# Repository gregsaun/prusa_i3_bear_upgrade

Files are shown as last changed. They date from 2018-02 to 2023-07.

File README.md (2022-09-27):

# Bear Frame Upgrade 2.1

## Table of contents
  1. [Introduction](#introduction)
  1. [Features](#features)
  1. [New features since Bear Frame 2.0](#new-features-since-bear-frame-20)
  1. [Compatibility](#compatibility)
  1. [Printed parts](#printed-parts)
  1. [Print settings](#print-settings)
  1. [Assembly guide](#assembly-guide)
  1. [Bill of materials](#bill-of-materials)
  1. [Optional parts](#optional-parts)
  1. [Community](#community)
  1. [Official distributors](#official-distributors)
  1. [Partners and contributors](#partners-and-contributors)
  1. [Support my work](#support-my-work)
  1. [Thank you](#thank-you)
  1. [License](#license)
  1. [Credit, sources and inspiration](#credit-sources-and-inspiration)

## Introduction

The Bear Frame Upgrade improves stiffness and reliability of the original [Prusa i3 MK2(S), MK2.5(S)(S+) and MK3(S)(S+)](https://www.prusa3d.com/). It allows faster prints, increases precision, makes maintenance easier and opens the door to more customisations. Plus it looks unique with our coloured frames!

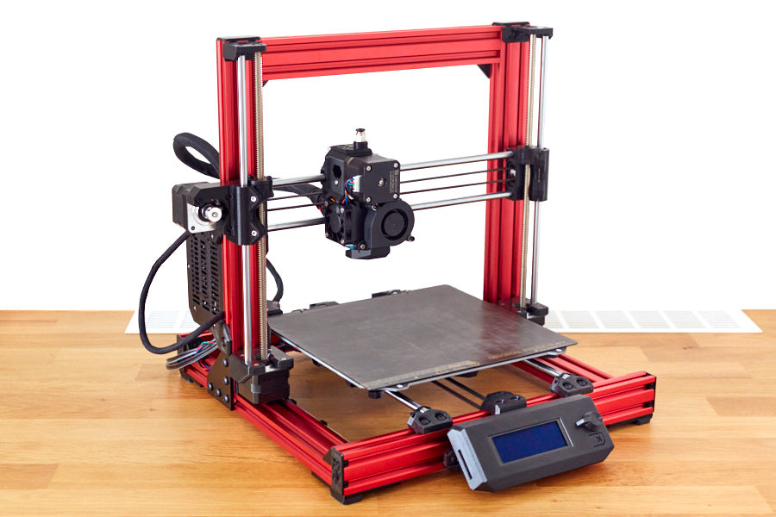
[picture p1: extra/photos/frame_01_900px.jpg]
Bear Frame Upgrade 2.1 MK3S


## Features

  * Compatible with Original Prusa i3 MK2(S), MK2.5(S) and MK3(S)(S+)
  * Compatible with lots of extruders like Original Prusa, BearExxa, BearMera (E3D Hemera) and Bondtech Prusa Upgrade
  * Reuse of as many parts as possible
  * Sturdy frame for faster printing
  * High quality extrusions
  * Custom, sturdier t-nuts
  * Improved accuracy
  * Reduced noise level
  * Easy to use and maintain
  * Built to last
  * Precisely engineered printed parts
  * Thoroughly tested development
  * Highly customisable
  * Detailed documentation via [guides.bear-lab.com](https://guides.bear-lab.com/)
  * Compatible with stock firmware (only if you use the Original Prusa extruder)
  * Active and open minded community
  * Truly open source

## New features since Bear Frame 2.0

  * Improved assembly guide and documentation (via [guides.bear-lab.com](https://guides.bear-lab.com/))
  * Single frame for all Prusa versions (same frame as Full Bear 2.0 MK3)
  * New stiffer Y axis with tensioner
  * New stiffer Z axis
  * Improved X and Y axis homing accuracy
  * Improved Z axis alignment and assembly
  * Reduced Y axis stepper noise for MK3(S)
  * New build helpers for Y and Z axis
  * Support for all Prusa PSUs
  * Custom, sturdier t-nuts
  * Shorter LCD supports
  * New custom LCD cover
  * Nicer and more resistant end caps
  * Easier assembly of printed parts
  * Improved wire management with new cable clips
  * Stiffer mounts for Rambo Mini/Einsy cover
  * Compatible with E3D Gates idlers as well as 9mm belt

## Compatibility

This Bear Frame Upgrade 2.1 is compatible with the Full Bear Frame Upgrade 2.0 __MK3__ frame. If you do not know which frame you have please check [our FAQ here](https://guides.bear-lab.com/Wiki/Bear_FAQ#Section_Which_Full_Bear_frame_do_I_have). The 2.1 version needs extra hardware (screws, nuts, washers, dowel pin), check the [bill of materials](doc/bom.md) for more details. You can also order hardware upgrade kit from our [distributor websites](#official-distributors).

:bulb: If you have a Full Bear Frame Upgrade 2.0 MK2S or MK2.5 frame you can find compatible parts in the [optional parts section](#optional-parts) below.

:warning: The new Y and Z axis are __not__ compatible with any of the existing Prusa or Bear 2.0 parts. You have to update all parts from Bear 2.1.

:warning: The original Prusa firmware is compatible with the Bear Upgrade 2.1 only if you use the Original Prusa extruder and X axis. If you use the Bear upgrade 2.1 frame with BearExxa, BearMera or Bondtech extruders you will need to use custom firmware.

## Printed parts

:bulb: All links here correspond to the latest stable release.

:warning: Warning: It is important to follow the recommended print settings and to **calibrate your extrusion multiplier** before printing the parts (for each and every spool that you use). [Check our calibration guide here](https://guides.bear-lab.com/Guide/Extrusion+multiplier+and+filament+diameter/8).

**Printed parts:**
  * Bear Frame 2.1 for MK3(S)(S+) STL files: [bear21_mk3-3s_stl.zip](../../releases/latest/download/bear21_mk3-3s_stl.zip)
  * Bear Frame 2.1 for MK2(S) or MK2.5(S) STL files: [bear21_mk2-2s-25-25s_stl.zip](../../releases/latest/download/bear21_mk2-2s-25-25s_stl.zip)
  * Bear Frame 2.1 optional parts (check [optional parts section](#optional-parts) below) files: [bear21_optional_parts.zip](../../releases/latest/download/bear21_optional_parts.zip)

**CAD, drawings and source files**:
  * Bear 2.1 frame for MK3(S)(S+) CAD files and mechanical drawings: [bear21_cad_drawings_files.zip](../../releases/latest/download/bear21_cad_drawings_files.zip)
  * All source files (this complete repository): Go the to latest release [here](../../releases/latest) and in the bottom of the release note, under the Assets, click on "Source code" (you can choose between zip and tar.gz files).

## Print settings

:warning: Warning: It is important to follow the recommended print settings and to **calibrate your extrusion multiplier** before printing the parts (for each and every spool that you use). [Check our calibration guide here](https://guides.bear-lab.com/Guide/Extrusion+multiplier+and+filament+diameter/8).

[Read the print settings here](doc/print_settings.md).

## Assembly guide

[Read the assembly guide here](https://guides.bear-lab.com/c/Frame).

## Bill of materials

[Read the BOM here](doc/bom.md).

## Optional parts

#### Official optional parts

| Description | Link |
|---|---|
| Upgrade parts for Bear 2.0 MK2(S), MK2.5(S) frame | [bear_2.0_upgrade_mk2-2s-2.5-2.5s](optional_parts/bear_2.0_upgrade_mk2-2s-2.5-2.5s/README.md) |
| LCD cover | [lcd_cover](optional_parts/lcd_cover/README.md) |
| MMU2(S) frame holder adapter | [mmu2_adapter](optional_parts/mmu2_adapter/README.md) |
| Y idler for larger 9mm 2GT belt | [y_idler_9mm_belt](optional_parts/y_idler_9mm_belt/README.md) |
| Y idler tensioner for E3D idler | [y_idler_tensioner_e3d](optional_parts/y_idler_tensioner_e3d/README.md) |
| Bear Extruder and X Axis | [Bear Extruder and X axis for MK2.5S MK3S](https://github.com/gregsaun/bear_extruder_and_x_axis) |

#### Community's optional parts

Find optional parts designed by the community at [guides.bear-lab.com/Wiki/community_optional_parts](https://guides.bear-lab.com/Wiki/community_optional_parts).

## Community

Here are the places were The Bear project is the most active on:

* Discord server of "The 602 Wasteland" community : [discordapp.com/invite/hYUjSnW](https://discordapp.com/invite/hYUjSnW)
* Facebook group : [facebook.com/groups/PrusaBearUpgrade](https://www.facebook.com/groups/PrusaBearUpgrade)
* Twitter : [@gregoiresaunier](https://twitter.com/gregoiresaunier)
* GitHub : [github.com/gregsaun](https://github.com/gregsaun)

Do not hesitate to ask if you have a question.

## Official distributors

Official distributors are selling the official bear kit with all screws, our custom t-nuts and extrusions ready for the upgrade from an Original Prusa, you will only need to print 3D printed parts.

  * 3dboom.es logo  
    3D Boom (EU)  
    [3dboom.es](http://www.3dboom.es)  

  * lecktor logo  
    Lecktor (EU)  
    [lecktor.com](http://lecktor.com)  

  * makerparts.ca logo  
    Makerparts.ca (CA)  
    [makerparts.ca](http://makerparts.ca)  

  * ooznest logo  
    Ooznest (UK)  
    [ooznest.co.uk](https://ooznest.co.uk/)  

  * printed solid logo  
    Printed Solid (US)  
    [printedsolid.com](https://www.printedsolid.com/)  

By purchasing a kit from official distributors you are supporting the development of the Bear project, thank you very much :heart: !

## Partners and contributors

LDO Motors &nbsp;[LDO Motors](http://ldomotors.com/) is the manufacturer of the official Bear frame upgrade kit for all distributors.

3DFused &nbsp;[3DFused](https://3dfused.com/) is helping the Bear development team with linear motion knowledge and will sell custom linear rail kit for the Bear Frame Upgrade.

Grégoire Saunier is the original designer of the Bear Frame Upgrade and Extruder.

Bendix Sørensen, David Ogles, Florian Däubler, Josh Jones and Stefan Maue are active contributors.

Barry Danks, David Ogles, Florian Däubler, Josh Jones, Nathan Denkin, Orlando from All3DMakers and Termlimit are admins of the Bear community and help with documentation.

## Support my work

The bear project is made possible thanks to its supporters. You can participate via
<br/><br/>
become a patron (https://www.patreon.com/gregsaun)<br/>[patreon.com/gregsaun](https://www.patreon.com/gregsaun)
<br/><br/>
paypal.me (https://www.paypal.me/gregsaun)<br/>[paypal.me/gregsaun](https://www.paypal.me/gregsaun)
<br/><br/>
You can also send me a tip via [Thingiverse](https://www.thingiverse.com/pekcitron/about) if you prefer.

Massive thank you in advance :heart:

## Thank you

Massive thank you to [Adrian Bowyer](https://github.com/AdrianBowyer/) for having invented [RepRap](http://reprapltd.com).

Thank you to all [my Patreon's](https://guides.bear-lab.com/Wiki/Bear_Supporters)

Thank you to Bendix Sørensen, David Ogles, Florian Däubler, Jason from LDO Motors, Nathan Denkin, Orlando from All3DMakers, Sleene, Termlimit, Josh Jones and Stefan Maue for helping me in developing the Bear project and for their beautiful support to the community.

Thank you to all that have sent me a tip on Thingiverse and PayPal.

Thank you to everybody from our Facebook group and The 602 Wasteland community.

Thank you for having purchased a kit from an official distributor.

Thank you to all official distributors for taking care of the kits and customers.

Thank you Jason from LDO Motors for the quality manufacturing and relationship.

Thank you Openbuilds<sup>&reg;</sup> for your hardware, community and state of mind.

Thank you for making the community alive with all your comments, issues, pull requests, optional parts, make, pictures, etc.

## License

All files in this repository are licensed under the GPLv3 license (unless otherwise noted). Here is a quick summary; for more details please check the LICENSE file.

What you __can__ do:
  * Modify
  * Distribute
  * Private, commercial and patent use

What you __must__ do:
  * Include copyright notice
  * Include a copy of the license
  * Share source files
  * Use the same license (GPLv3)
  * Document changes applied

Note: STL and STEP files are generally not source files. The source files are those you use to design your project such as CAD files (Fusion 360), mechanical drawings, code, documentation, etc. However, STL and STEP files are a commonly used format with great interoperability. Therefore, we encourage to share the STL and STEP files in addition to the source files.

## Credit, sources and inspiration

  * [Adrian Bowyer](https://github.com/AdrianBowyer/) for having invented [RepRap](http://reprapltd.com).
  * Original Prusa i3 printers: [prusa3d.com](http://www.prusa3d.com).
  * Prusa 3030 Haribo Edition: [github.com/PrusaMK2Users/3030_Haribo_Edition](https://github.com/PrusaMK2Users/3030_Haribo_Edition).
  * Openbuilds<sup>&reg;</sup> for the invention of open source V-Slot<sup>&reg;</sup> extrusions : [openbuilds.org](https://www.openbuilds.org).
  * Roy Henriksson for the inspiration of his Y axis tensioner : [thingiverse.com/thing:3502543](https://www.thingiverse.com/thing:3502543).
  * Vecko Kojchevski for his Z axis parts and feedback : [thingiverse.com/vekoj/designs](https://www.thingiverse.com/vekoj/designs).

Massive thanks to these persons and projects, without them the Bear could not exist!

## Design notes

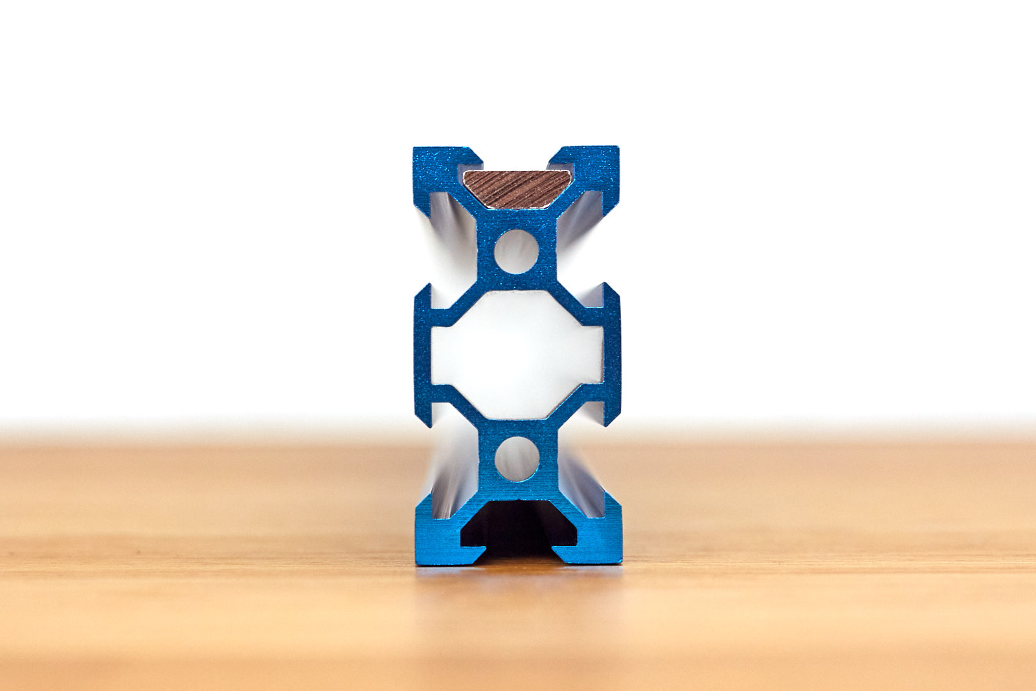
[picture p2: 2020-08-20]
extra/photos/hardware_08.jpg

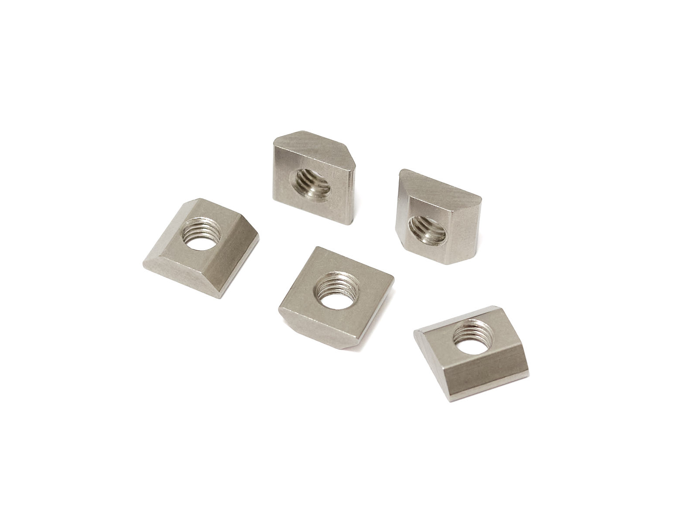
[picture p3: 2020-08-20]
extra/photos/hardware_02.jpg

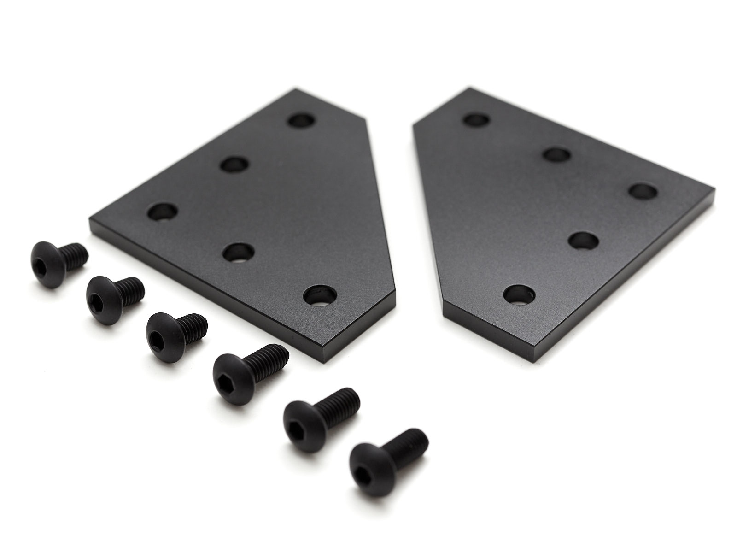
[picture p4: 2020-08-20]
extra/photos/hardware_03.jpg

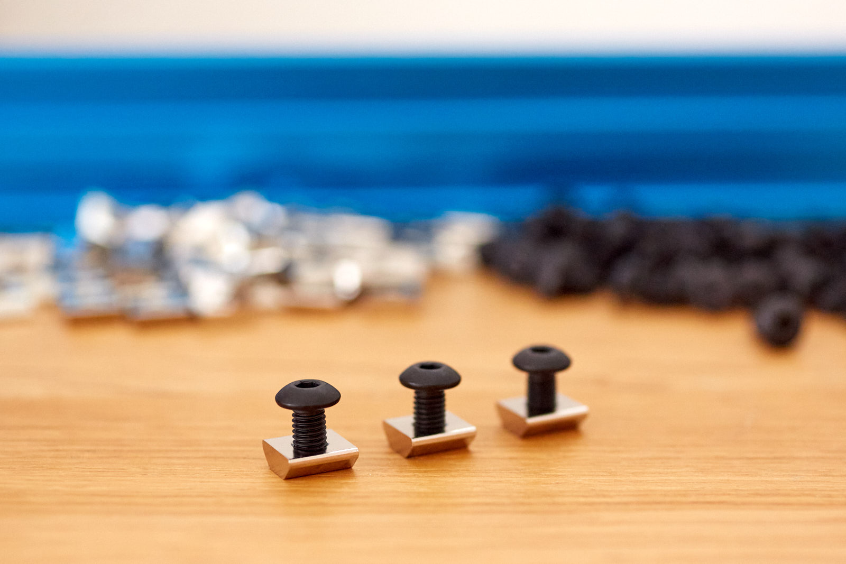
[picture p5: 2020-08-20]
extra/photos/hardware_06.jpg

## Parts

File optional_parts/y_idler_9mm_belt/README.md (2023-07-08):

# Bear Frame Upgrade 2.1

## Y idler for 9mm belts

### Introduction

This is a Y idler for 9mm wide Gates 2GT belt (standard is 6mm). Larger belts will have less flex and might reduce ringing.

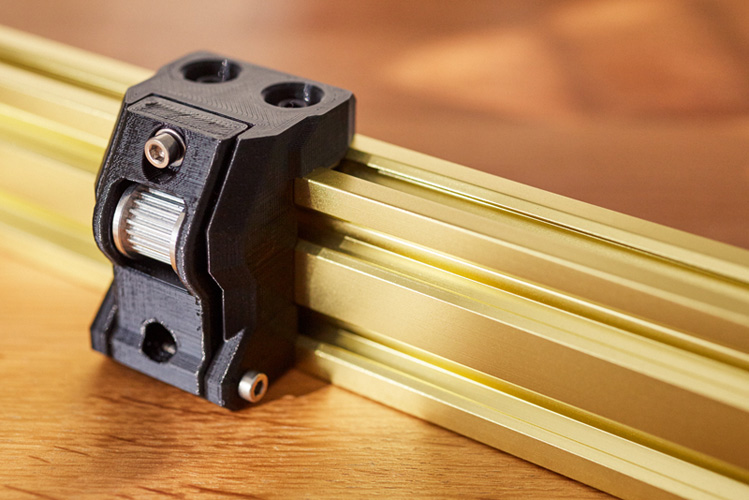
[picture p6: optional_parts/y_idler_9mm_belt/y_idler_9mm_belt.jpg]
Y idler for 9mm 2GT belt


### Bill of Materials

| Part | Quantity | Detail |
|---|:---:|---|
| E3D Gates 2GT 9mm Belt | 1 | [E3D store link](https://e3d-online.com/gates-powergripr-gt2-belt-9mm-x-100mm) |
| E3D Gates 2GT Toothed Idler<br/>9mm Belt, 20 Tooth, 5mm bore | 1 | [E3D store link](https://e3d-online.com/products/gates-belts-pulleys-and-idlers?variant=41205372420155) |
| 2GT Pulley 16T, 5mm bore | 1 | [Aliexpress Powge store](https://www.aliexpress.com/item/32995138803.html) |
| Dowel pin<br/>diameter: 4.90-4.95mm<br/>length: 20mm | 1 | Must fit the 2GT idler bearing.<br/>:pushpin: Cut a M5 screw if you can't find one |
| M3x30mm socket head screw ISO 4762 | 1 | |
| M3x25mm socket head screw ISO 4762 | 1 | |
| M3 Hex nylock nuts (DIN 985) | 2 | |
| M3 steel washer DIN 125, 0.5mm thick | 1 | |

### Printed parts

:pushpin: If you have any doubt as to which Bear frame you have, please check the [Bear FAQ here](https://guides.bear-lab.com/Wiki/Bear_FAQ#Section_Which_Bear_frame_do_I_have).

:warning: Warning: It is important to follow the recommended print settings and to **calibrate your extrusion multiplier** before printing the parts (for each and every spool that you use). [Check our calibration guide here](https://guides.bear-lab.com/Guide/Extrusion+multiplier+and+filament+diameter/8).

| Part | Qty | Note | Download link |
|---|:---:|---|---|
| y_belt_holder_9mm_belt_bear2.0_mk2s-2.5-2.5s | 1 | :warning: For Bear 2.0 MK2(S), MK2.5(S) frame | [y_belt_holder_9mm_belt_bear2.0_mk2s-2.5-2.5s.stl](printed_parts/y_belt_holder_9mm_belt_bear2.0_mk2s-2.5-2.5s.stl?raw=true) |
| y_belt_holder_9mm_belt_bear2.1_mk2s-2.5-2.5s | 1 | :warning: For Bear 2.1 MK2(S), MK2.5(S) frame | [y_belt_holder_9mm_belt_bear2.1_mk2s-2.5-2.5s.stl](printed_parts/y_belt_holder_9mm_belt_bear2.1_mk2s-2.5-2.5s.stl?raw=true) |
| y_belt_holder_9mm_belt_bear2.1_mk3-3s | 1 | :warning: For Bear 2.1 MK3(S) frame | [y_belt_holder_9mm_belt_bear2.1_mk3-3s.stl](printed_parts/y_belt_holder_9mm_belt_bear2.1_mk3-3s.stl?raw=true) |
| y_idler_mount_9mm_belt | 1 | | [y_idler_mount_9mm_belt.stl](printed_parts/y_idler_mount_9mm_belt.stl?raw=true) |
| y_idler_tensioner_9mm_belt | 1 | | [y_idler_tensioner_9mm_belt.stl](printed_parts/y_idler_tensioner_9mm_belt.stl?raw=true) |

The Y motor mount from the standard Bear Frame 2.1 printed parts is reused.

### Print settings

:warning: Warning: It is important to follow the recommended print settings and to **calibrate your extrusion multiplier** before printing the parts (for each and every spool that you use). [Check our calibration guide here](https://guides.bear-lab.com/Guide/Extrusion+multiplier+and+filament+diameter/8).

  * Slicer : PrusaSlicer recommended
  * Infill type : Gyroid recommended
  * Support : No
  * Brim : No
  * Detect thin walls : No
  * Perimeters width (internal and external) : 0.45mm

| Part | Layer<br/>Height<br/>[mm] | Infill [%] | Num.<br/>Perimeters | Num.<br/>Top/Bottom<br/>Layers |
|:-----|:---:|:---:|:---:|:---:|
| y_belt_holder_9mm_belt_X | 0.20 | 20 | 4 | 5 |
| y_idler_mount_9mm_belt | 0.20 | 20 | 4 | 5 |
| y_idler_tensioner_9mm_belt | 0.20 | 20 | 4 | 5 |

### Assembly instructions

Follow the same assembly instructions as for the standard Bear 2.1 Y idler.

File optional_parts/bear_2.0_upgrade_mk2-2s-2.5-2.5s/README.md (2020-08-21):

# Bear Frame Upgrade 2.1

## Bear 2.1 upgrade parts for use on an original Full Bear 2.0 MK2(S)/MK2.5(S) frame

### Table of contents
  1. [Introduction](#introduction)
  1. [Printed parts](#printed-parts)
  1. [Print settings](#print-settings)
  1. [Assembly guide](#assembly-guide)
  1. [Bill of materials](#bill-of-materials)

### Introduction

These parts allow you to upgrade your __Full Bear 2.0 MK2(S)/MK2.5(S) frame__ to use similar parts to, and with the same features as, the Bear 2.1 parts. The new Bear 2.1 frame is based on the Full Bear 2.0 MK3 frame which has (some) different extrusion lengths to the Full Bear 2.0 MK2(S)/MK2.5(S) frame.

These parts are __not__ compatible with the __Bear 2.1 frame for Prusa MK2(S)/MK2.5(S)__.

### Printed parts

To confirm that you have a __Full Bear 2.0 MK2(S)/MK2.5(S) frame__, you just need to check the length of the Y axis extrusions.

Measure the length of your Y axis __extrusion__ as shown in the diagram below.
  * If the length is __311 mm__ (±1mm):
    * Then you have a __Full Bear 2.0 MK2(S)/MK2.5(S) frame__.
    * You will need to use these parts: [Download this ZIP file](../../../../releases/latest/download/bear21_optional_parts.zip), STL are in the folder `bear_2.0_upgrade_mk2-2s-2.5-2.5s/printed_parts/stl`.
  * If the length is __331 mm__ (±1mm):
    * Then you have a frame compatible with the Bear 2.1 parts. You do __not__ need to use any of the parts linked above. Download the printed parts from the [links on the main, Bear 2.1, page](../../README.md#printed-parts).

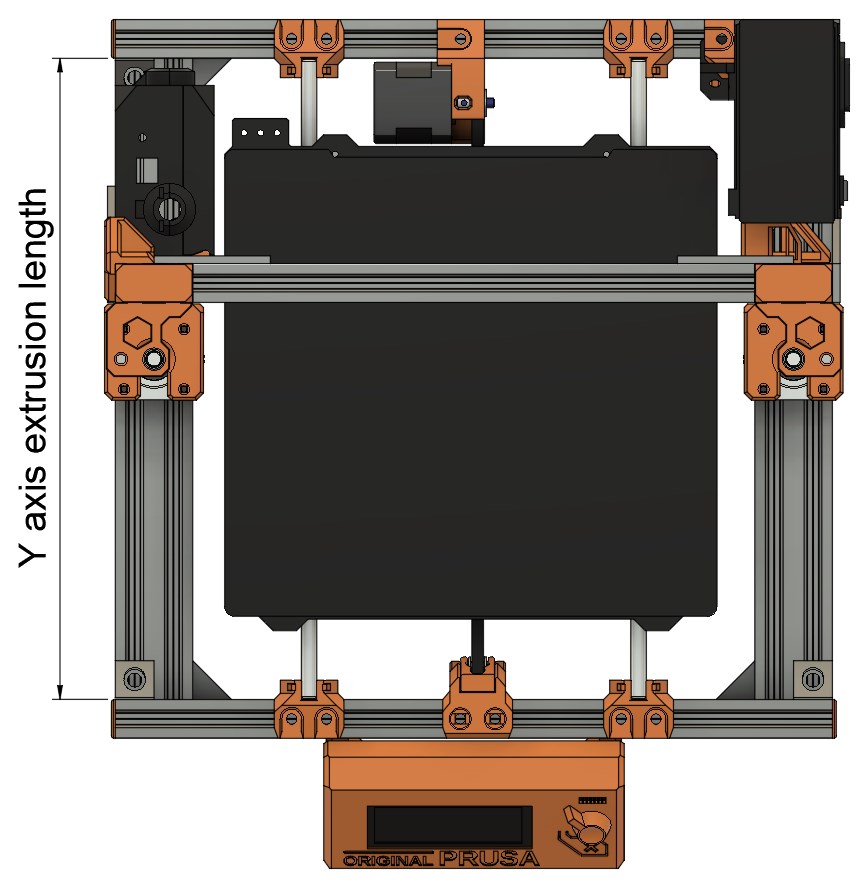
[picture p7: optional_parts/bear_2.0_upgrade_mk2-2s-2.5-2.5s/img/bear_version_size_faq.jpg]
Bear version frame size


### Print settings

:warning: Warning: It is important to follow the recommended print settings and to **calibrate your extrusion multiplier** before printing the parts (for each and every spool that you use). [Check our calibration guide here](https://guides.bear-lab.com/Guide/Extrusion+multiplier+and+filament+diameter/8).

Use the same print settings as for the Bear Frame 2.1 parts: [link to the print settings](../../doc/print_settings.md).

### Assembly guide

Use the same assembly guide as for the Bear Frame 2.1: [link to the assembly guide](https://guides.bear-lab.com/c/Frame).

### Bill of materials

The BOM is the same as for the Bear Frame 2.1: [link to the bom](../../doc/bom.md).

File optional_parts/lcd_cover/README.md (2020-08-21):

# Bear Frame Upgrade 2.1

## LCD Cover

### Table of contents
  1. [Introduction](#introduction)
  1. [Pictures](#pictures)
  1. [Compatibility](#compatibility)
  1. [Bill of materials](#bill-of-materials)
  1. [Printed parts](#printed-parts)
  1. [Print settings](#print-settings)

### Introduction

This is an alternative LCD cover designed for the Bear Frame Upgrade.
  * New accurate design from scratch
  * Shorter frame thanks to a bevel at the front (4th picture)
  * Elimination of vibrations by using 4 screws to attach the LCD
  * Easier rotation of the LCD knob
  * Faster to print while using less filament
  * Sleek design for better look
  * Improved design for best print quality
  * Optional: LCD supports compatible with stock Prusa MK3(S) frame
  * Available in several looks:
      * Simple without text or logo
      * Bear logo
      * Bear Upgrade text
      * Bear logo and text
      * Bear Paw logo

:bulb: The Bear Paw logo is a special design for the LGBT community because it is one of their symbols. You can find more details about it here: https://en.wikipedia.org/wiki/Bear_flag_(gay_culture)

### Pictures

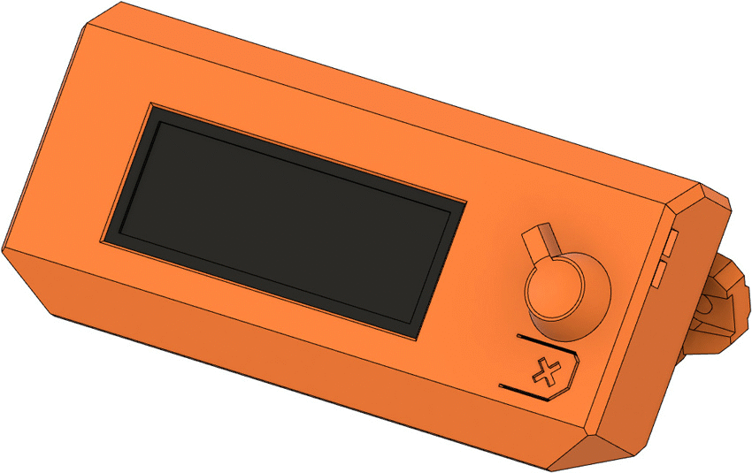
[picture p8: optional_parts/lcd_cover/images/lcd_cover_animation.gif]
LCD Cover Animation


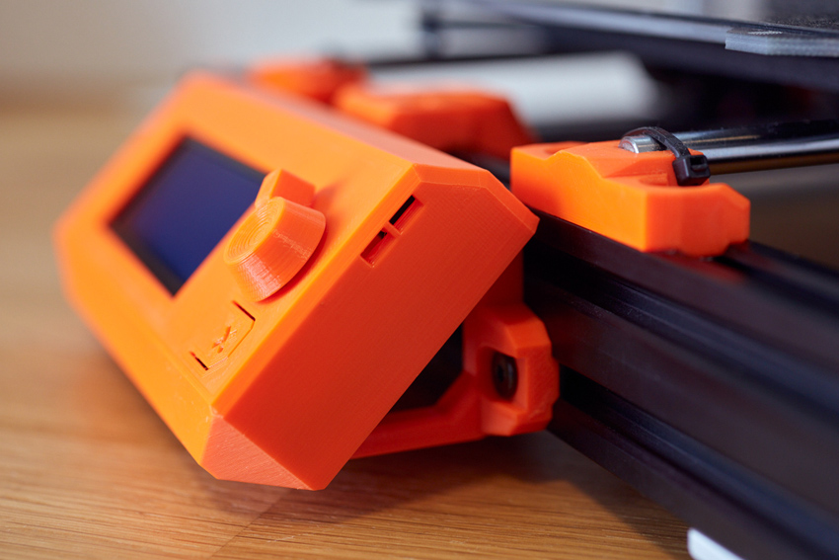
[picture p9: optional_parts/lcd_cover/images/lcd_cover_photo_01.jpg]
LCD Cover Photo speaker holes


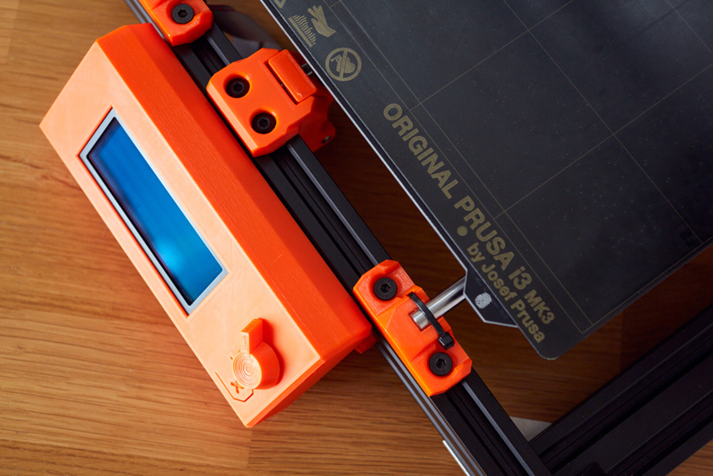
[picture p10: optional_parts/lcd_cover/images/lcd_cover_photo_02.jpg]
LCD Cover Photo top view


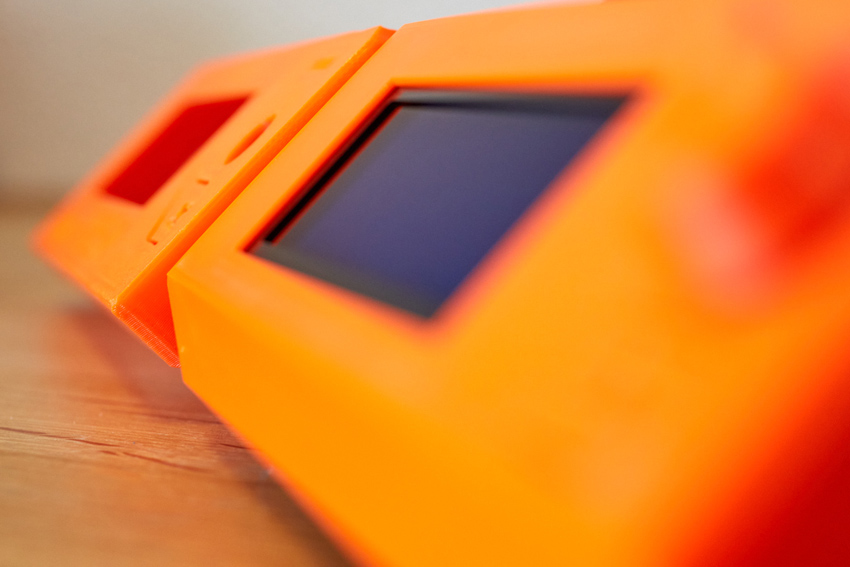
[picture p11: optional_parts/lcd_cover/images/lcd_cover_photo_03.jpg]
LCD Cover Photo bevel


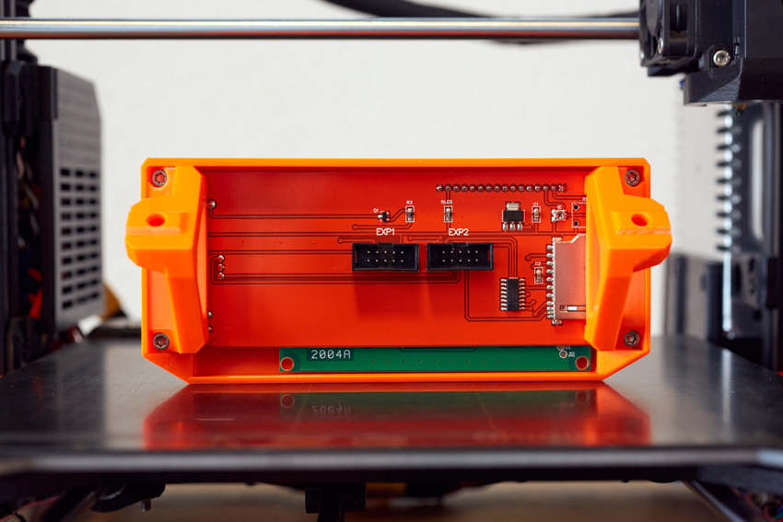
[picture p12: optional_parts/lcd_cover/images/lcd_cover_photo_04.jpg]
LCD Cover Photo screw mount


# Compatibility

This Bear LCD cover is compatible with all Bear Frame Upgrades. It is also compatible with the Original Prusa MK3(S) frame (see section [Printed parts](#printed-parts)).

### Bill of materials

| Part | Quantity | Detail |
|---|:---:|---|
| Original Prusa LCD unit | 1 | [Prusa store link](https://shop.prusa3d.com/en/spare-parts/213-lcd-unit.html) |
| M3x10mm socket head screw ISO 4762 | 4 | |

### Printed parts

| Part | Qty | Note | Download link |
|---|:---:|---|---|
| lcd_cover | 1 |  Choose one of the available designs (check the GIF on top) | [lcd_cover.stl](printed_parts/stl/lcd_cover.stl?raw=true)<br>[lcd_cover_text.stl](printed_parts/stl/lcd_cover_text.stl?raw=true)<br>[lcd_cover_logo.stl](printed_parts/stl/lcd_cover_logo.stl?raw=true)<br>[lcd_cover_logo_text.stl](printed_parts/stl/lcd_cover_logo_text.stl?raw=true)<br>[lcd_cover_lgbt_bear_paw.stl](printed_parts/stl/lcd_cover_lgbt_bear_paw.stl?raw=true) |
| lcd_knob | 1 | | [lcd_knob.stl](printed_parts/stl/lcd_knob.stl?raw=true) |
| lcd_support_a | 1 | For **Bear frame** | [lcd_support_a.stl](printed_parts/stl/lcd_support_a.stl?raw=true) |
| lcd_support_b | 1 | For **Bear frame** | [lcd_support_b.stl](printed_parts/stl/lcd_support_b.stl?raw=true) |
| lcd_support_a_prusa | 1 | For **Original Prusa frame** | [lcd_support_a_prusa.stl](printed_parts/stl/lcd_support_a_prusa.stl?raw=true) |
| lcd_support_b_prusa | 1 | For **Original Prusa frame** | [lcd_support_b_prusa.stl](printed_parts/stl/lcd_support_b_prusa.stl?raw=true) |

### Print settings

:warning: Warning: It is important to follow the recommended print settings and to **calibrate your extrusion multiplier** before printing the parts (for each and every spool that you use). [Check our calibration guide here](https://guides.bear-lab.com/Guide/Extrusion+multiplier+and+filament+diameter/8).

  * Slicer : PrusaSlicer recommended
  * Infill type : Gyroid recommended
  * Support : No
  * Brim : No
  * Detect thin walls : No
  * Perimeters width : 0.45mm

| Part | Layer<br/>Height<br/>[mm] | Infill [%] | Num.<br/>Perimeters | Num.<br/>Top/Bottom<br/>Layers |
|:-----|:---:|:---:|:---:|:---:|
| lcd_cover | 0.20 | 20 | 3 | 5 |
| lcd_support | 0.20 | 20 | 3 | 5 |
| lcd_knob | 0.20 | 20 | 3 | 5 |

### Credit

The bear paw logo has been designed by Solipandi Designs: https://www.etsy.com/listing/487103775/bear-paw-svg-cut-files-svg-and-dxf-cut

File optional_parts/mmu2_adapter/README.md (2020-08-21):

# Bear Frame Upgrade 2.1

## MMU2(S) Frame Holder for Bear Frame

### Table of contents
  1. [Introduction](#introduction)
  1. [Pictures](#pictures)
  1. [Compatibility](#compatibility)
  1. [Bill of materials](#bill-of-materials)
  1. [Printed parts](#printed-parts)
  1. [Print Settings](#print-settings)

### Introduction

MMU2 and MMU2S frame holder for the Bear Frame Upgrade.

### Pictures

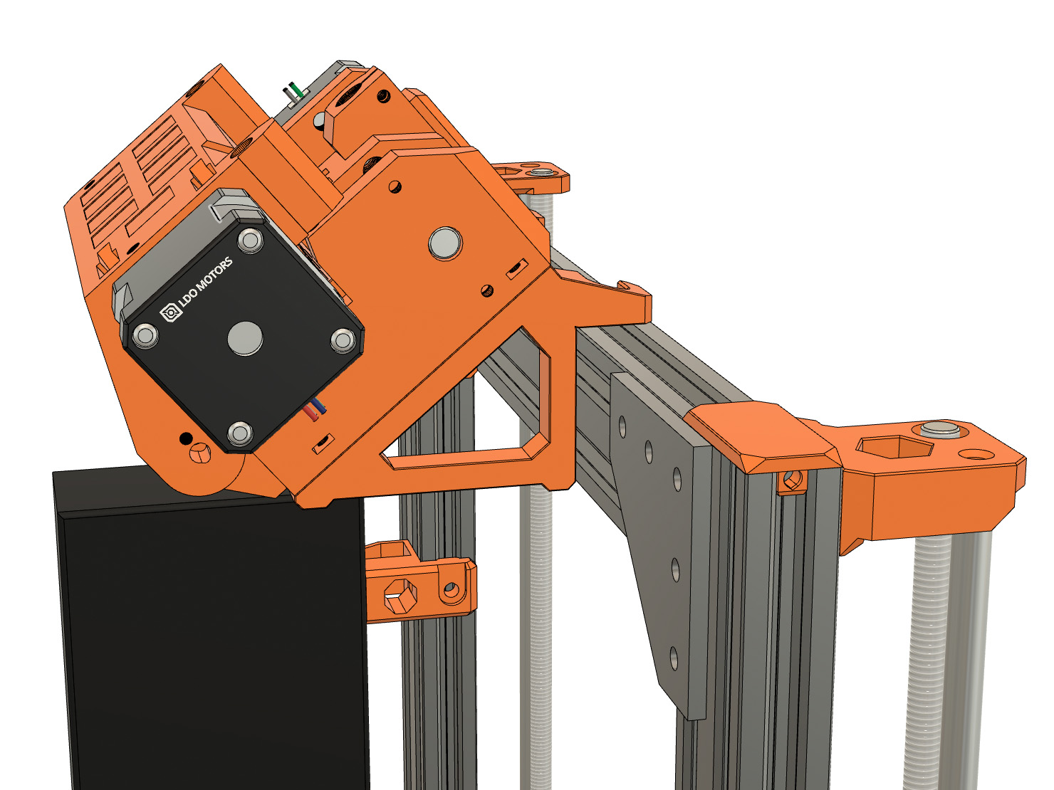
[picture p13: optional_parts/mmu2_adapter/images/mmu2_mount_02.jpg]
MMU2(S) mount


MMU2(S) mount

### Compatibility

This MMU2(S) frame holder is compatible with both MMU2 and MMU2S.

### Bill of materials

| Part | Quantity | Example |
|---|:---:|---|
| M5x10mm button head screw (ISO 7380) | 2 | |
| Drop-in tee-nuts M5 | 2 | [Openbuilds](https://openbuildspartstore.com/spring-loaded-tee-nuts/) |

### Printed parts

:warning: Warning: It is important to follow the recommended print settings and to **calibrate your extrusion multiplier** before printing the parts (for each and every spool that you use). [Check our calibration guide here](https://guides.bear-lab.com/Guide/Extrusion+multiplier+and+filament+diameter/8).

Use this link to download the STL: [mmu2_frame_holder.stl](printed_parts/mmu2_frame_holder.stl?raw=true)

### Print settings

:warning: Warning: It is important to follow the recommended print settings and to **calibrate your extrusion multiplier** before printing the parts (for each and every spool that you use). [Check our calibration guide here](https://guides.bear-lab.com/Guide/Extrusion+multiplier+and+filament+diameter/8).

  * Slicer : PrusaSlicer recommended
  * Infill type : Gyroid recommended
  * Support : No
  * Brim : No
  * Detect thin walls : No
  * Perimeters width (internal and external) : 0.45mm

| Layer Height | Infill | Perimeters | Top/Bottom Layers |
|:---:|:---:|:---:|:---:|
| 0.20mm | 20% | 3-4 | 5 |

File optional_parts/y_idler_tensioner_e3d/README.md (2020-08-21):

# Bear Frame Upgrade 2.1

## Y idler tensioner for E3D toothed idler

### Introduction

This is a Y idler tensioner compatible with the E3D toothed idler

Bear 2.1 Idler Tensioner for E3D Gates pulleys

### Bill of Materials

| Part | Quantity | Detail |
|---|:---:|---|
| E3D Gates 2GT Toothed Idler<br/>6mm Belt, 20 Tooth, 5mm ID | 1 | [E3D store link](https://e3d-online.com/products/gates-powergrip%C2%AE-2gt-idlers) |
| Dowel pin<br/>diameter: 4.90-4.95mm<br/>length: 15.8mm | 1 | Must fit the 2GT idler bearing.<br/>:pushpin: Cut a M5 screw if you can't find one |
| M3x30mm socket head screw ISO 4762 | 1 | |
| M3x25mm socket head screw ISO 4762 | 1 | |
| M3 Hex nylock nuts (DIN 985) | 2 | |
| M3 steel washer DIN 125, 0.5mm thick | 1 | |

### Printed Parts

:warning: Warning: It is important to follow the recommended print settings and to **calibrate your extrusion multiplier** before printing the parts (for each and every spool that you use). [Check our calibration guide here](https://guides.bear-lab.com/Guide/Extrusion+multiplier+and+filament+diameter/8).

| Part | Quantity | Download link |
|---|:---:|---|
| y_idler_mount<br/>(from standard Bear 2.1 printed parts) | 1 | [y_idler_mount.stl](../../printed_parts/common_to_all_versions/stl/y_idler_mount.stl?raw=true) |
| y_idler_tensioner_e3d<br/>(from this page) | 1 | [y_idler_tensioner_e3d.stl](printed_parts/y_idler_tensioner_e3d.stl?raw=true) |

### Print Settings

:warning: Warning: It is important to follow the recommended print settings and to **calibrate your extrusion multiplier** before printing the parts (for each and every spool that you use). [Check our calibration guide here](https://guides.bear-lab.com/Guide/Extrusion+multiplier+and+filament+diameter/8).

* Filament type: PETG
* Slicer: PrusaSlicer
* Infill type : Gyroid recommended
* Support : No
* Brim : No
* Detect thin walls : No
* Perimeters width (internal and external) : 0.45mm

| Part | Layer<br/>Height<br/>[mm] | Infill [%] | Num.<br/>Perimeters | Num.<br/>Top/Bottom<br/>Layers |
|:-----|:---:|:---:|:---:|:---:|
| y_idler_mount | 0.20 | 20 | 4 | 5 |
| y_idler_tension_e3d | 0.20 | 20 | 4 | 5 |

### Assembly instructions

Follow the same assembly instructions as for the standard Bear 2.1 Y idler.

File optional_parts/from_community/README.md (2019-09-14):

# Bear Upgrades 2.1

## Optional parts made by the community

Designed by the community. Huge thank you all :heart: !

| Description | Author | Link |
|---|---|---|
| Spool holder | Christopher Burgess | https://www.thingiverse.com/thing:2846383 |
| Spool holder | Kappa Mi | https://www.thingiverse.com/thing:3068093 |
| Spool holder | Martin Majewski | https://www.thingiverse.com/thing:3142106 |
| Multi Material Adapter for MMU 1.0 | Karel Koci | https://www.thingiverse.com/thing:2831583 |
| Raspberry Pi 3B case | Mat Unter | https://www.thingiverse.com/thing:2869086 |
| Bear Logo LCD cover | Tom Bergman | https://www.thingiverse.com/thing:2941711 |
| SD-Card Holder V-Slot Extrusion | D. Meyer | https://www.thingiverse.com/thing:3198211 |
| Mean Well LRS-350 PSU Case | Matthew Humphrey | https://www.thingiverse.com/thing:3180564 |
| Universal Zaribo Einsy Box | Juan Puchol | https://www.thingiverse.com/thing:3239428/ |
| Ocie's Duet Wifi Enclosure Box remix | George Harrison | https://www.thingiverse.com/thing:3642653 |
| LED Light Mounts | Joe Mike Terranella | https://www.thingiverse.com/thing:3619763 |
| X Axis to Y Rod Calibration Tool | Peter Bauer | https://www.thingiverse.com/thing:3645355 |

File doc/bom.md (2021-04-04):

# Bear Frame Upgrade 2.1

## Bill of Materials

### Hardware

| Part | Quantity | Detail | Example Links |
|---|:---:|---|---|
| Original Prusa i3 MK2(S) or MK2.5(S) or MK3(S)(S+) | 1 | | [Prusa](https://www.prusa3d.com) |
| V-Slot 20x40 331mm | 2  | | [Openbuilds](http://openbuildspartstore.com/v-slot-20x40-linear-rail/) |
| V-Slot 20x40 359mm | 2  | | [Openbuilds](http://openbuildspartstore.com/v-slot-20x40-linear-rail/) |
| V-Slot 20x40 370mm | 2  | | [Openbuilds](http://openbuildspartstore.com/v-slot-20x40-linear-rail/) |
| V-Slot 20x40 290mm | 1  | | [Openbuilds](http://openbuildspartstore.com/v-slot-20x40-linear-rail/) |
| Black angle corner | 4  | | [Openbuilds](http://openbuildspartstore.com/black-angle-corner-connector/) |
| 90 degree joining plate | 10 | | [Openbuilds](http://openbuildspartstore.com/90-degree-joining-plate/) |
| Tee-nuts M5 | 88 | 50x for 90° plates,<br> 8x for angle corner,<br> 30x for printed parts | [Openbuilds](http://openbuildspartstore.com/tee-nuts-10-pack/) |
| M5x8mm button head screw (ISO 7380)  | 12 | 8x for angle corner,<br>4x printed parts | [Openbuilds](http://openbuildspartstore.com/low-profile-screws-m5-10-pack/)<br>[McMaster-Carr](https://www.mcmaster.com/#91239a222/=1clymbr)|
| M5x10mm button head screw (ISO 7380) | 62 | 46x for 90° plates,<br> 16x for printed parts<br> | [Openbuilds](http://openbuildspartstore.com/low-profile-screws-m5-10-pack/)<br>[McMaster-Carr](https://www.mcmaster.com/#97763a820/=1cltxg0) |
| M5x12mm button head screw (ISO 7380) | 13 | 1x for Y motor mount,<br>8x for Y rod holders,<br>4x for feet | [Openbuilds](http://openbuildspartstore.com/low-profile-screws-m5-10-pack/)<br>[McMaster-Carr](https://www.mcmaster.com/#91239a228/=1cm065c) |
| M5x16mm button head screw (ISO 7380) | 1  | 1x for Y motor mount | [McMaster-Carr](https://www.mcmaster.com/92095a212) |
| M3x14mm socket head screw (ISO 4762) | 2  | 2x RAMBo base mounts | [McMaster-Carr](https://www.mcmaster.com/91292a027) |
| M3x18mm socket head screw (ISO 4762) | 3  | 3x Y motor mount | [McMaster-Carr](https://www.mcmaster.com/91292a029) |
| M3x25mm socket head screw (ISO 4762) | 7  | 1x for Y idler, 6x for Y bearing holders | [McMaster-Carr](https://www.mcmaster.com/91292a020) |
| M3x30mm socket head screw (ISO 4762) | 1  | 1x for Y idler | [McMaster-Carr](https://www.mcmaster.com/91292a022) |
| Set screw M4x5mm | 12 | for end_caps | [McMaster-Carr](https://www.mcmaster.com/92015a111) |
| Dowel pin<br/>dia: 2.90-2.95mm<br/>length: 15.8-16mm | 1 | :pushpin: Cut a M3 screw if you can't find one | |
| M3 hex nuts DIN 934 | 2  | 2x for Rambo base mounts | [McMaster-Carr](https://www.mcmaster.com/91828a211) |
| M3 nylock nut DIN 985 | 2  | 2x for Y idler | [McMaster-Carr](https://www.mcmaster.com/93625a100) |
| M3 square nut DIN 562 | 2  | 1x for Y belt holder, 1x for lower PSU mount | |
| M3 flat washer (ISO 7089) | 2  | 1x for Y idler | |
| Zip ties 2.5x100mm | 30 | | |

A full BOM with all parts to build a Bear from scratch has been made by [Chris Riley](https://www.youtube.com/channel/UCqRiv7rQuxge63bqJ2hVNUQ) and [3D_Gussner](https://github.com/3d-gussner), you can find it here: https://docs.google.com/spreadsheets/d/1AKX1dBssPeFiCTYAHjYHZiUIhAR5COqE82Bq8tjKFSE/edit?usp=sharing . Massive thank you to Chris and 3D_Gussner!

### Printed Parts

| Part | Quantity | Comment |
|---|:---:|---|
| build_helper_y | 1 | :warning: Print a single part |
| build_helper_z | 1 | :warning: Print a single part |
| cable_clip_horizontal  | 2 | |
| cable_clip_lcd | 5 | |
| cable_clip_vertical | 6 | |
| foot | 4 | |
| lcd_support_a | 1 | |
| lcd_support_b | 1 | |
| psu_lower_mount | 1 | File name may vary depending your PSU version |
| psu_upper_mount | 2 | File name may vary depending your PSU version |
| rambo_base_lower_mount | 1 | |
| rambo_base_upper_mount | 1 | |
| rambo_hinge_lower | 1 | File name may vary depending your printer version |
| rambo_hinge_upper | 1 | File name may vary depending your printer version |
| y_bearing_holder | 3 | |
| y_belt_holder | 1 | |
| y_end_caps | 2 | Total of 4 printed parts |
| y_idler_mount | 1 | |
| y_idler_tensioner | 1 | |
| y_motor_endstop_mount  | 1 | :warning: Only for MK2(S) or MK2.5(S) |
| y_motor_mount | 1 | |
| y_rod_holder | 4 | |
| z_end_caps | 1 | Total of 2 printed parts |
| z_leadscrew_cap | 2 | |
| z_motor_mounts | 1 | Total of 2 printed parts |
| z_tops | 1 | Total of 2 printed parts |

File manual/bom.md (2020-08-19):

# Bear Frame Upgrade 2.1

## Bill of Materials

### Hardware

| Part | Quantity | Detail | Example Links |
|---|:---:|---|---|
| Original Prusa i3 MK2(S) or MK2.5(S) or MK3(S) | 1 | | [Prusa](https://www.prusa3d.com) |
| V-Slot 20x40 331mm | 2 | | [Openbuilds](http://openbuildspartstore.com/v-slot-20x40-linear-rail/) |
| V-Slot 20x40 359mm | 2 | | [Openbuilds](http://openbuildspartstore.com/v-slot-20x40-linear-rail/) |
| V-Slot 20x40 370mm | 2 | | [Openbuilds](http://openbuildspartstore.com/v-slot-20x40-linear-rail/) |
| V-Slot 20x40 290mm | 1 | | [Openbuilds](http://openbuildspartstore.com/v-slot-20x40-linear-rail/) |
| Black angle corner | 4 | | [Openbuilds](http://openbuildspartstore.com/black-angle-corner-connector/) |
| 90 degree joining plate | 10 | | [Openbuilds](http://openbuildspartstore.com/90-degree-joining-plate/) |
| Tee-nuts M5 | 88 | 50x for 90° plates,<br> 8x for angle corner,<br> 30x for printed parts | [Openbuilds](http://openbuildspartstore.com/tee-nuts-10-pack/) |
| M5x8mm button head screw (ISO 7380) | 12 | 8x for angle corner,<br>4x printed parts | [Openbuilds](http://openbuildspartstore.com/low-profile-screws-m5-10-pack/)<br>[McMaster-Carr](https://www.mcmaster.com/#91239a222/=1clymbr)|
| M5x10mm button head screw (ISO 7380) | 62 | 46x for 90° plates,<br> 16x for printed parts<br> | [Openbuilds](http://openbuildspartstore.com/low-profile-screws-m5-10-pack/)<br>[McMaster-Carr](https://www.mcmaster.com/#97763a820/=1cltxg0) |
| M5x12mm button head screw (ISO 7380) | 13 | 1x for Y motor mount,<br>8x for Y rod holders,<br>4x for feet | [Openbuilds](http://openbuildspartstore.com/low-profile-screws-m5-10-pack/)<br>[McMaster-Carr](https://www.mcmaster.com/#91239a228/=1cm065c) |
| M5x16mm button head screw (ISO 7380) | 1 | 1x for Y motor mount | [McMaster-Carr](https://www.mcmaster.com/92095a212) |
| M3x14mm socket head screw (ISO 4762) | 2 | 2x RAMBo base mounts | [McMaster-Carr](https://www.mcmaster.com/91292a027) |
| M3x18mm socket head screw (ISO 4762) | 3 | 3x Y motor mount | [McMaster-Carr](https://www.mcmaster.com/91292a029) |
| M3x25mm socket head screw (ISO 4762) | 7 | 1x for Y idler, 6x for Y bearing holders | [McMaster-Carr](https://www.mcmaster.com/91292a020) |
| M3x30mm socket head screw (ISO 4762) | 1 | 1x for Y idler | [McMaster-Carr](https://www.mcmaster.com/91292a022) |
| Set screw M4x5mm | 12 | for end_caps | [McMaster-Carr](https://www.mcmaster.com/92015a111) |
| Dowel pin<br/>diameter: 2.90-2.95mm<br/>length: 15.8mm to 16mm | 1 | :pushpin: Cut a M3 screw if you can't find one | |
| M3 hex nuts DIN 934 | 2 | 2x for Rambo base mounts | [McMaster-Carr](https://www.mcmaster.com/91828a211) |
| M3 nylock nut DIN 985 | 2 | 2x for Y idler | [McMaster-Carr](https://www.mcmaster.com/93625a100) |
| M3 square nut DIN 562 | 2 | 1x for belt holder, 1x for lower PSU mount | |
| Zip ties 2.5x100mm | 30 | | |

We recommend to use thread locker like Loctite Blue 243 to secure screws during assembly (for metal thread to metal thread, not metal thread to plastic).

A full BOM with all parts to build a Bear from scratch has been made by [Chris Riley](https://www.youtube.com/channel/UCqRiv7rQuxge63bqJ2hVNUQ) and [3D_Gussner](https://github.com/3d-gussner), you can find it here: https://docs.google.com/spreadsheets/d/1AKX1dBssPeFiCTYAHjYHZiUIhAR5COqE82Bq8tjKFSE/edit?usp=sharing . Massive thank you to Chris and 3D_Gussner!

### Printed Parts

| Part | Quantity | Comment |
|---|:---:|---|
| build_helper_z | 1 | |
| build_helper_y | 1 | |
| y_end_caps | 2<br/>(total of 4 parts) | |
| z_end_caps | 1<br/>(total of 2 parts) | |
| foot | 4 | |
| lcd_support_a | 1 | |
| lcd_support_b | 1 | |
| psu_lower_mount | 1 | same for black and silver PSU versions |
| psu_upper_mount | 2 | same for black and silver PSU versions |
| rambo_base_lower_mount | 1 | |
| rambo_base_upper_mount | 1 | |
| rambo_lid_lower_hinge  | 1 | |
| rambo_lid_upper_hinge  | 1 | |
| y_bearing_holder | 3 | |
| y_belt_holder | 1 | |
| y_idler_tensioner | 1 | |
| y_idler_mount | 1 | |
| y_motor_mount | 1 | |
| y_motor_endstop_mount  | 1 | :warning: Only for MK2S or MK2.5(S) |
| y_rod_holder | 4 | |
| z_leadscrew_cap | 2 | 0.20 | 20 | 2 | 5 | |
| z_motor_mounts | 1<br/>(total of 2 parts) | |
| z_tops | 1<br/>(total of 2 parts) | |
| cable_clip_horizontal  | 2 | |
| cable_clip_vertical | 6 | |
| cable_clip_lcd | 5 | |

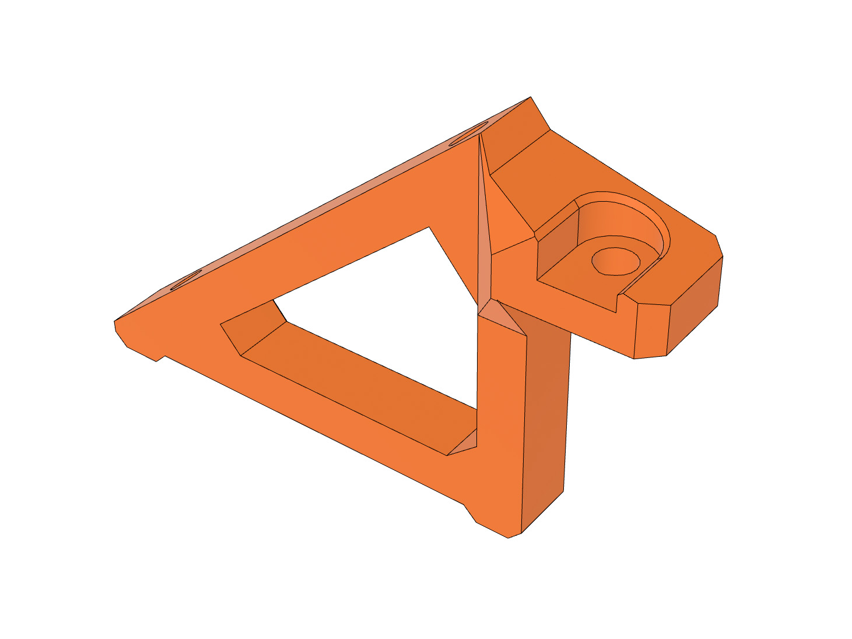
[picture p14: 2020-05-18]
optional_parts/mmu2_adapter/images/mmu2_mount_01.jpg

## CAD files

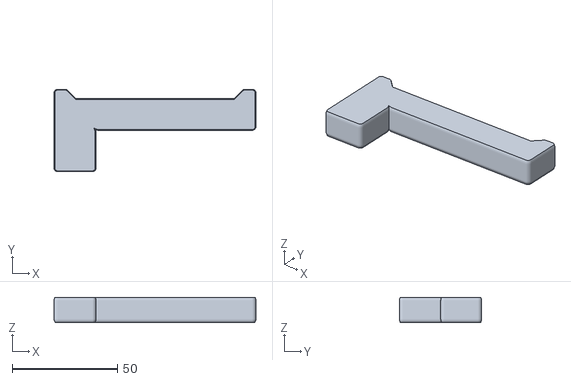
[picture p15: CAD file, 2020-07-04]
optional_parts/bear_2.0_upgrade_mk2-2s-2.5-2.5s/printed_parts/stl/build_helper_z_96mm.stl
96.0 x 39.2 x 12.0

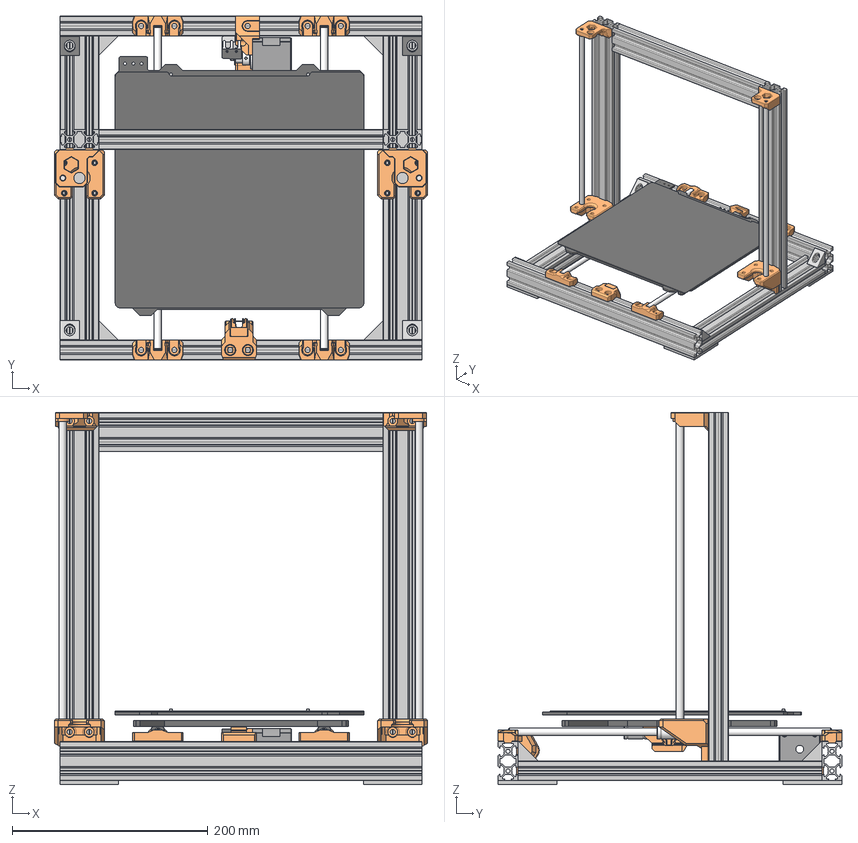
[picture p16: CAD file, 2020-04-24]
optional_parts/bear_2.0_upgrade_mk2-2s-2.5-2.5s/source/bear_2.0_mk2_upgrade_to_2.1.step
381.0 x 351.0 x 380.2 mm
vslot_front_rear x 2
vslot_y x 2
Joining Plate 90 Degree x 4
Black Angle Corner Connector x 4
y_rod_holder x 4
y_carriage_mk2
heatedbed_mk52_12v
steel_sheet_mk3
lm8uu x 3
y_rod x 2
y_motor_mount_1
nema17_ldo_xye
2gt_pulley_16t_6mmbelt
y_motor_endstop_mount
end_stop
y_idler_tensioner
y_idler_mount
2gt_idler_20t_6mmbelt
y_belt_holder_1
vslot_z x 2
vslot_z_top
z_motor_mount
z_motor_mount v1(Mirror)
z_rod x 2
z_top
z_top v1(Mirror)

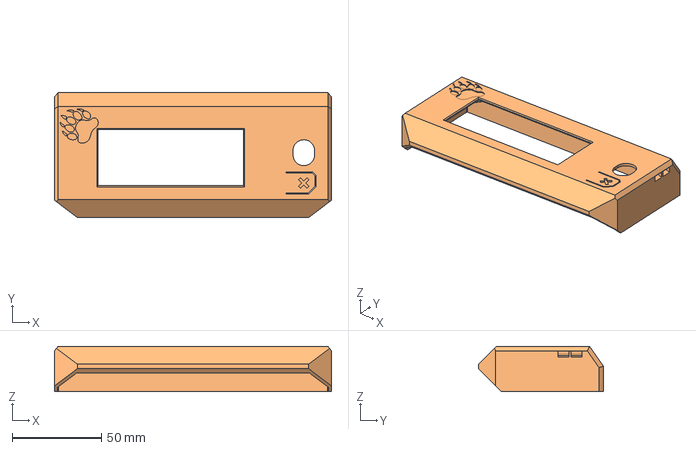
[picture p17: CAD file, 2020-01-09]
optional_parts/lcd_cover/cad_files/lcd_cover_lgbt_bear_paw.step
155.0 x 70.0 x 25.4 mm

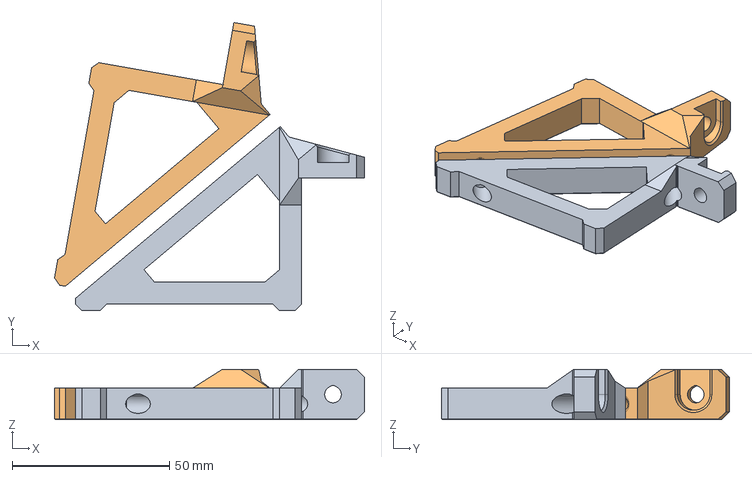
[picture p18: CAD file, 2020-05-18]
optional_parts/mmu2_adapter/cad_files/mmu2_frame_holder.step
98.4 x 91.4 x 16.0 mm
mmu2_frame_holder_left
mmu2_frame_holder_right

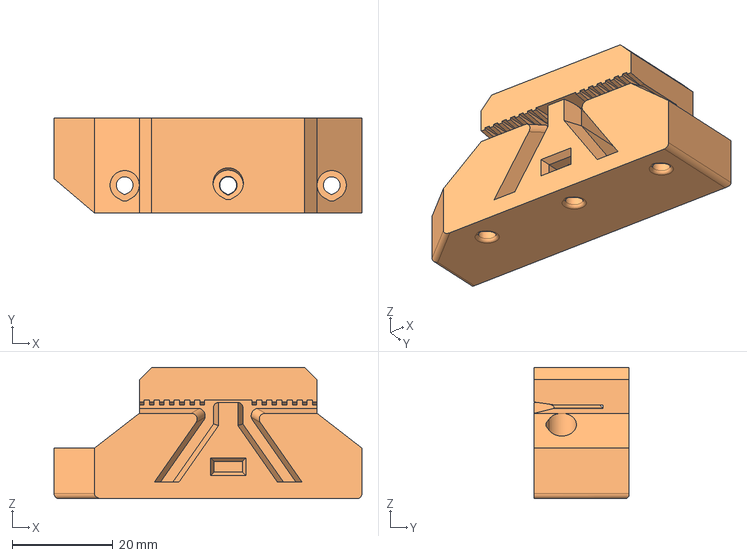
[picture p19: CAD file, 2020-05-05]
optional_parts/y_idler_9mm_belt/cad_files/y_belt_holder_9mm_belt_bear2.1_mk2s-2.5-2.5s.step
61.0 x 18.8 x 26.0 mm

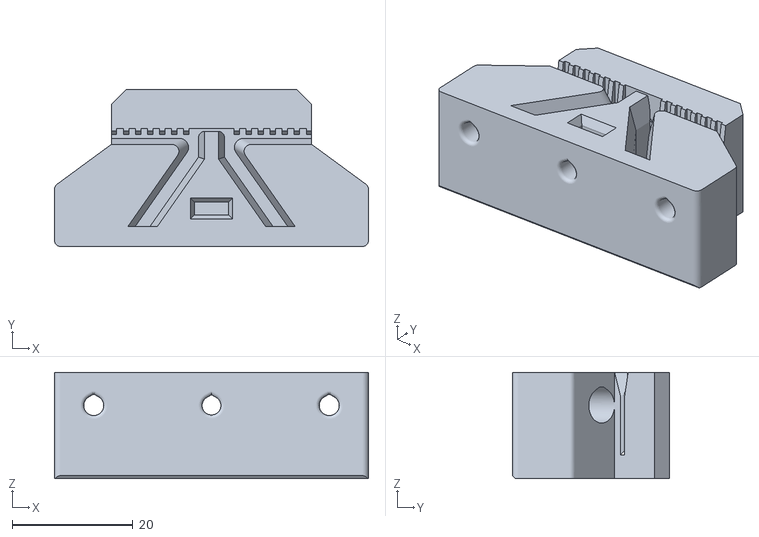
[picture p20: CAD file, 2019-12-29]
optional_parts/y_idler_9mm_belt/printed_parts/y_belt_holder_9mm_belt_bear2.1_mk3-3s.stl
52.0 x 26.0 x 17.6

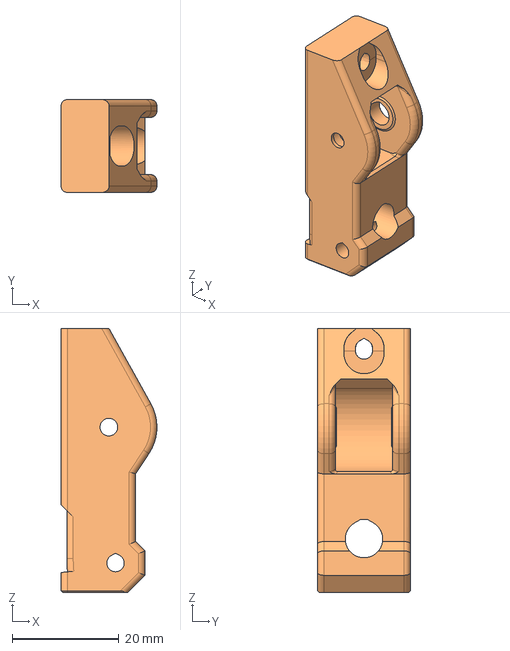
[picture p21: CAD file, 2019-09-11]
optional_parts/y_idler_tensioner_e3d/cad_files/y_idler_tensioner_e3d.step
17.9 x 17.4 x 49.4 mm

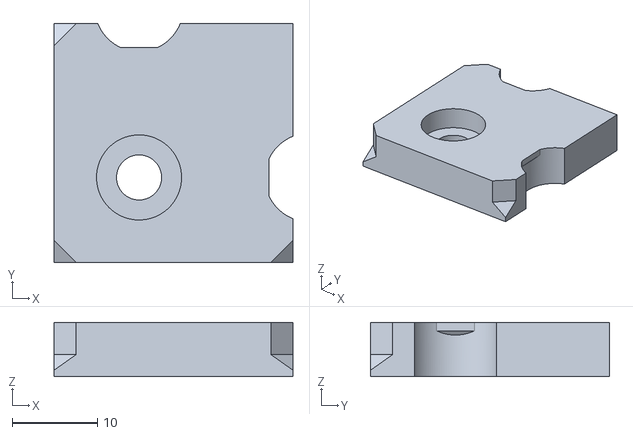
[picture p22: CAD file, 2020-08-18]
printed_parts/common_to_all_versions/stl/foot.stl
28.1 x 28.1 x 6.40

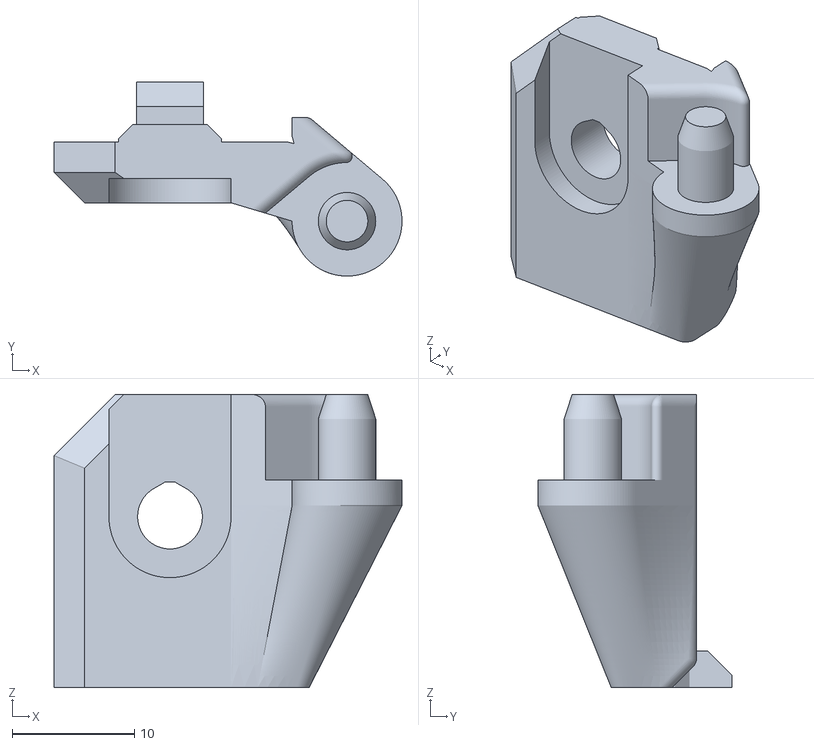
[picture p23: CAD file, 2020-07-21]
printed_parts/mk3_mk3s/stl/rambo_hinge_lower.stl
28.5 x 15.9 x 24.0

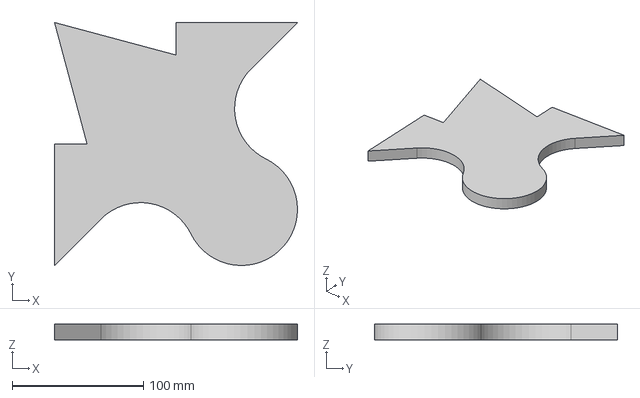
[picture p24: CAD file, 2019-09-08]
test/ringing_vfa/ringing_vfa_01.step
185.0 x 185.0 x 12.0 mm

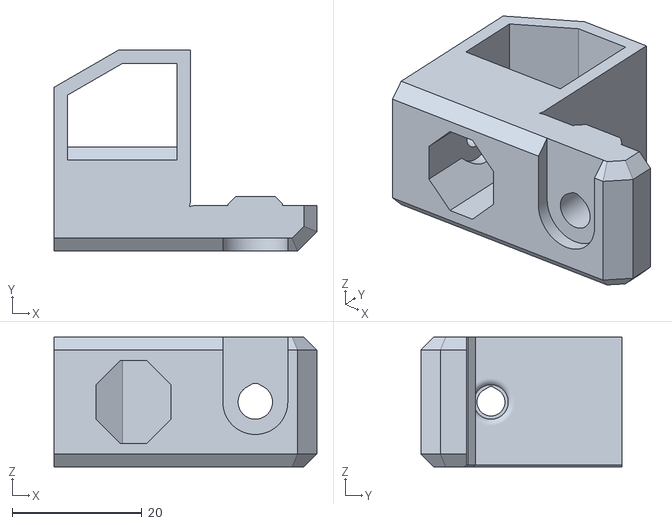
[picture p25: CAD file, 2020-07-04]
optional_parts/bear_2.0_upgrade_mk2-2s-2.5-2.5s/printed_parts/stl/psu_upper_mount.stl
40.5 x 31.0 x 20.0

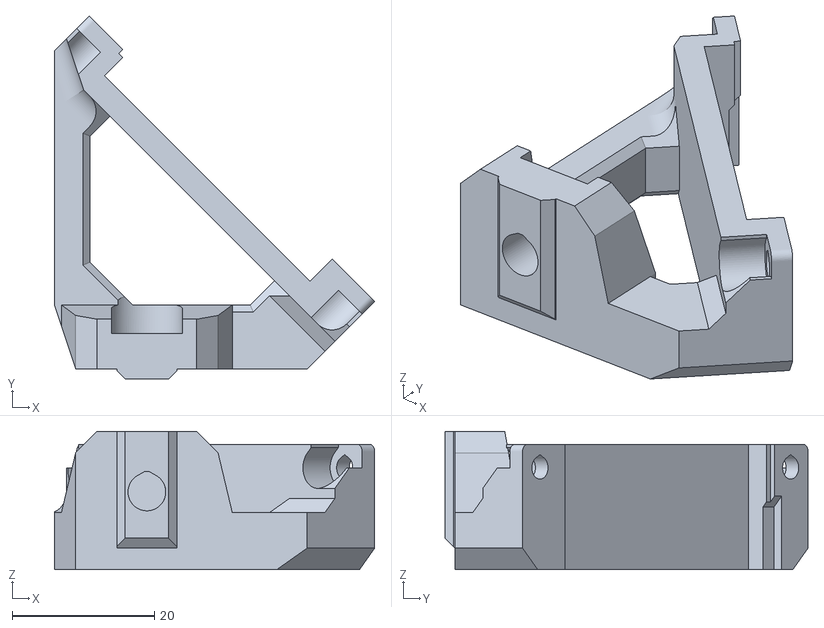
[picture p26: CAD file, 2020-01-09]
optional_parts/lcd_cover/printed_parts/stl/lcd_support_b.stl
45.0 x 51.0 x 19.4

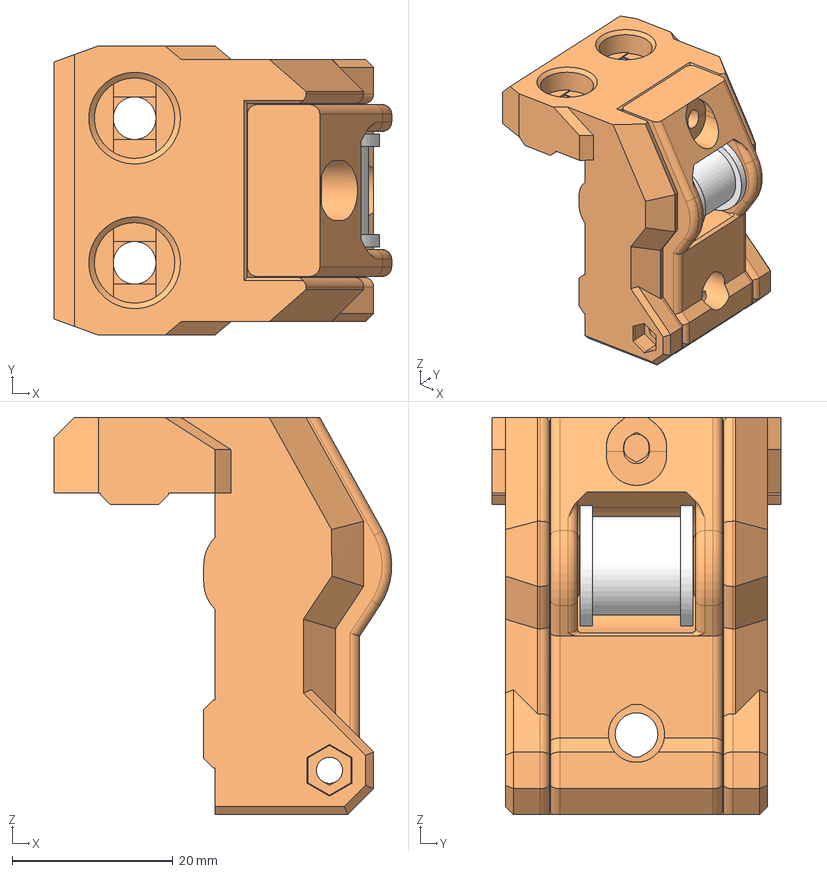
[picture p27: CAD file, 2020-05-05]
optional_parts/y_idler_9mm_belt/cad_files/y_idler_9mm_belt.step
42.0 x 36.0 x 49.4 mm
e3d_2gt_idler_20t_9mm_belt
dowel_pin

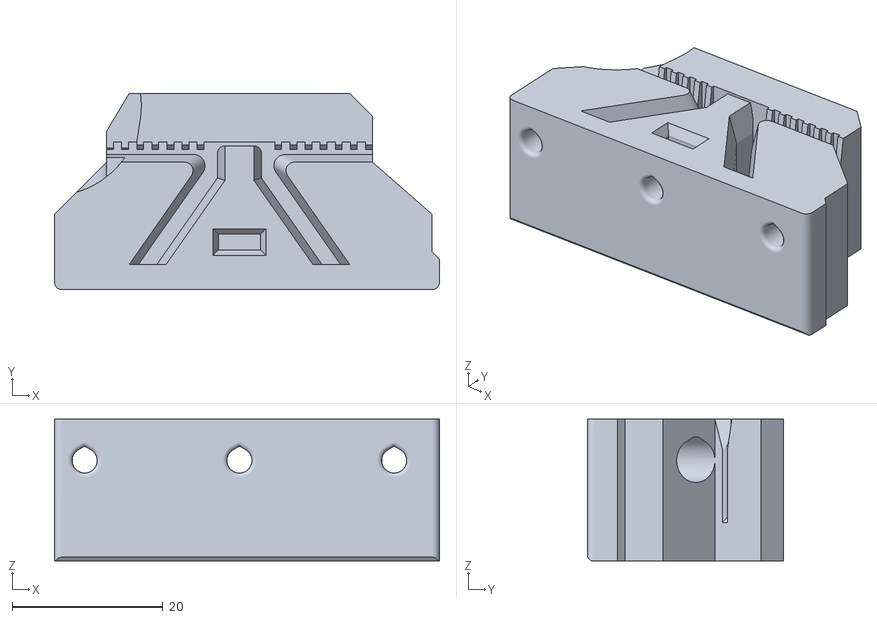
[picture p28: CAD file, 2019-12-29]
optional_parts/y_idler_9mm_belt/printed_parts/y_belt_holder_9mm_belt_bear2.0_mk2s-2.5-2.5s.stl
51.0 x 26.0 x 18.8

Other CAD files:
optional_parts/lcd_cover/printed_parts/stl/lcd_cover.stl
optional_parts/mmu2_adapter/printed_parts/mmu2_frame_holder.stl
optional_parts/y_idler_tensioner_e3d/printed_parts/y_idler_tensioner_e3d.stl
optional_parts/lcd_cover/cad_files/lcd_cover.step
optional_parts/bear_2.0_upgrade_mk2-2s-2.5-2.5s/printed_parts/stl/psu_lower_mount.stl
optional_parts/bear_2.0_upgrade_mk2-2s-2.5-2.5s/printed_parts/stl/y_belt_holder.stl
optional_parts/bear_2.0_upgrade_mk2-2s-2.5-2.5s/printed_parts/stl/y_rod_holder.stl
optional_parts/bear_2.0_upgrade_mk2-2s-2.5-2.5s/printed_parts/stl/z_motor_mounts.stl
optional_parts/bear_2.0_upgrade_mk2-2s-2.5-2.5s/printed_parts/stl/z_tops.stl
optional_parts/lcd_cover/cad_files/lcd_cover_assembly.f3z
optional_parts/lcd_cover/cad_files/lcd_cover_logo.step
optional_parts/lcd_cover/cad_files/lcd_cover_logo_text.step
optional_parts/lcd_cover/cad_files/lcd_cover_prusa.f3z
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

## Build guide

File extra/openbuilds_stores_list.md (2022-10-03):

# Distributors List

If a store in your country does not sell Pre-Cut V-Slots, try to send an email.

You can contribute to those tables using [this issue](https://github.com/gregsaun/prusa_i3_bear_upgrade/issues/4). Thanks!

## Official distributors

## Official distributors

Official distributors are selling the official bear kit with all screws, our custom t-nuts and extrusions ready for the upgrade from an Original Prusa, you will only need to print 3D printed parts.

  * 3dboom.es logo  
    3D Boom (EU)  
    [3dboom.es](http://www.3dboom.es)  

  * lecktor logo  
    Lecktor (EU)  
    [lecktor.com](http://lecktor.com)  

  * makerparts.ca logo  
    Makerparts.ca (CA)  
    [makerparts.ca](http://makerparts.ca)  

  * ooznest logo  
    Ooznest (UK)  
    [ooznest.co.uk](https://ooznest.co.uk/)  

  * printed solid logo  
    Printed Solid (US)  
    [printedsolid.com](https://www.printedsolid.com/)  

By purchasing a kit from official distributors you are supporting the development of the Bear project, thank you very much :heart: !

## Openbuilds distributors

Here is a list of stores that sell Openbuilds extrusion (V-Slot) and hardware. You will have to purchase all hardware separetely according to the bom (and sometimes you will need to cut to length the extrusion).

### Asia
| Location | Address | Pre-Cut | Comment | Review |
|:---:|:---:|:---:|:---:|:---:|
| India | [https://www.3dprintronics.com](https://www.3dprintronics.com/Aluminium-Extrusions-c7124102) | Y | | |
| Russia | https://soberizavod.ru/ | Y | Extrusion center hole is M6 not M5 | |

### Australia

| Location | Address | Pre-Cut | Comment | Review |
|:---:|:---:|:---:|:---:|:---:|
| Victoria | http://www.makerstore.com.au | N | | |

### Europe

| Location | Address | Pre-Cut | Comment | Review |
|:---:|:---:|:---:|:---:|:---:|
| Belgium | https://tronixmaker.com | Y | | |
| Denmark | https://3dnielsen.dk/ | Y | | |
| Estonia | http://lecktor.com | Y | Official kit distributor | | 
| France | http://www.vslot-europe.com | N | | |
| Germany | http://www.watterott.com | N | Not all Openbuilds parts are available | Cuts are not accurate (+/- 1mm)<br>Fast shipping |
| Greece | [https://grobotronics.com](https://grobotronics.com/mechanics-and-wheels/openbuilds-v-slot/) | N | | |
| Italia | http://www.openbuildsitalia.com | Y | | |
| Norway | [https://www.kjell.com/no](https://www.kjell.com/no/produkter/elektro-og-verktoy/elektronikk/aluminiumprofiler/ratrig-aluminiumsprofil-20-x-40-mm-100-cm-p88154) | ? | | |
| Poland | [https://blackfrog.pl](https://blackfrog.pl/set-of-aluminum-profiles-openb-prusa-i3-bear-mod-p-1306.html) | Y | Official kit distributor | |
| Portugal | http://www.ratrig.com | Y | Official kit distributor | |
| Russia | https://soberizavod.ru/ | Y | Extrusion center hole is M6 not M5 | |
| Spain | http://store.thingibox.com/en/ | Y | | |
| Sweden | [https://www.kjell.com/se/](https://www.kjell.com/se/sortiment/el-verktyg/elektronik/aluminiumprofiler/ratrig-aluminiumprofil-20x40-mm-50-cm-p88153) | ? | | |
| Switzerland | https://www.3dware.ch/ | N | | Okay, nothing special |
| UK | http://ooznest.co.uk/ | Y | Official kit distributo | |

### New Zealand

| Location | Address | Pre-Cut | Comment | Review |
|:---:|:---:|:---:|:---:|:---:|
| Auckland | http://www.cnckits.co.nz | N | | |

### North Africa

| Location | Address | Pre-Cut | Comment | Review |
|:---:|:---:|:---:|:---:|:---:|
| Algeria | http://www.dzduino.store | N | | |

### North America

| Location | Address | Pre-Cut | Comment | Review |
|:---:|:---:|:---:|:---:|:---:|
| Canada | https://makerparts.ca/ | Y | Official kit distributor | |
| Canada | [https://www.robotshop.com](https://www.robotshop.com/en/ratrig-black-aluminum-extrusion-20x40mm-1000mm.html) | N | | |
| Florida | http://all3dmakers.com/ | Y | Official kit distributor | |
| Mexico | https://openbuilds.com.mx | N | | |
| Mexico | http://www.spkautomatizacion.com | N | | |
| New Jersey | http://openbuildspartstore.com | N | | |
| New York | http://www.opensourceluthiersupply.com | N | | |
| ? | http://makerstore.cc | N | | |

### South America

| Location | Address | Pre-Cut | Comment | Review |
|:---:|:---:|:---:|:---:|:---:|
| Brazil | https://www.tdtec.com.br/ | N | You'll need to contact them to be sure of which other related components they sell, though | |
| Brazil | [https://www.mercadolivre.com.br](https://eshops.mercadolivre.com.br/tdtec) | N | You'll need to contact them to be sure of which other related components they sell, though | |

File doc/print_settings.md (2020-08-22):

# Bear Frame Upgrade 2.1

## Print Settings

:warning: Warning: It is important to follow the recommended print settings and to **calibrate your extrusion multiplier** before printing the parts (for each and every spool that you use). [Check our calibration guide here](https://guides.bear-lab.com/Guide/Extrusion+multiplier+and+filament+diameter/8).

* Filament type: PETG
* Slicer: PrusaSlicer
* Infill type : Gyroid recommended
* Support : No
* Brim : No
* Detect thin walls : No
* Perimeters width (internal and external) : 0.45mm

| Part | Quantity | Layer<br/>Height<br/>[mm] | Infill [%] | Num.<br/>Perimeters | Num.<br/>Top / Bottom<br/>Layers | Note |
|:-----|:---:|:---:|:---:|:---:|:---:|:-----|
| build_helper_y | 1 | 0.20 | 20 | 3 | 5 | :warning: Print a single part |
| build_helper_z | 1 | 0.20 | 20 | 3 | 5 | :warning: Print a single part |
| cable_clip_horizontal  | 2 | 0.20 | 20 | 4 | 5 | |
| cable_clip_lcd | 5 | 0.20 | 20 | 4 | 5 | |
| cable_clip_vertical | 6 | 0.20 | 20 | 4 | 5 | |
| foot | 4 | 0.20 | 20 | 3 | 5 | |
| lcd_support_a | 1 | 0.20 | 20 | 3 | 5 | |
| lcd_support_b | 1 | 0.20 | 20 | 3 | 5 | |
| psu_lower_mount | 1 | 0.20 | 20 | 3 | 5 | File name may vary depending your PSU version |
| psu_upper_mount | 2 | 0.20 | 20 | 3 | 5 | File name may vary depending your PSU version |
| rambo_base_lower_mount | 1 | 0.20 | 20 | 3 | 5 | |
| rambo_base_upper_mount | 1 | 0.20 | 20 | 3 | 5 | |
| rambo_hinge_lower | 1 | 0.20 | 20 | 3 | 5 | File name may vary depending your printer version |
| rambo_hinge_upper | 1 | 0.20 | 20 | 3 | 5 | File name may vary depending your printer version |
| y_bearing_holder | 3 | 0.20 | 20 | 5 | 5 | |
| y_belt_holder | 1 | 0.20 | 20 | 4 | 5 | |
| y_end_caps | 2 | 0.20 | 20 | 3 | 5 | Total of 4 printed parts |
| y_idler_mount | 1 | 0.20 | 20 | 4 | 5 | |
| y_idler_tensioner | 1 | 0.20 | 20 | 4 | 5 | |
| y_motor_endstop_mount  | 1 | 0.20 | 20 | 4 | 5 | :warning: Only for MK2(S) or MK2.5(S) |
| y_motor_mount | 1 | 0.20 | 20 | 4 | 5 | |
| y_rod_holder | 4 | 0.20 | 20 | 4 | 5 | |
| z_end_caps | 1 | 0.20 | 20 | 3 | 5 | Total of 2 printed parts |
| z_leadscrew_cap | 2 | 0.20 | 20 | 2 | 5 | |
| z_motor_mounts | 1 | 0.20 | 20 | 4 | 5 | Total of 2 printed parts |
| z_tops | 1 | 0.20 | 20 | 4 | 5 | Total of 2 printed parts |

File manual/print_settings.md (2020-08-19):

# Bear Frame Upgrade 2.1

## Print Settings

:warning: Warning: It is important to follow the recommended print settings and to **calibrate your extrusion multiplier** before printing the parts (for each and every spool you are going to use). [Check our calibration guide here](https://guides.bear-lab.com/Guide/Extrusion+multiplier+and+filament+diameter/8).

* Filament type: PETG
* Slicer: PrusaSlicer
* Infill type : Gyroid recommended
* Support : No
* Brim : No
* Detect thin walls : No
* Perimeters width (internal and external) : 0.45mm

| Part | Quantity | Layer<br/>Height<br/>[mm] | Infill<br/>[%] | Num.<br/>Perimeters | Num.<br/>Top/Bottom<br/>Layers | Note |
|:----|:----:|:----:|:----:|:----:|:----:|:----|
| build_helper_z | 1 | 0.20 | 15 | 3 | 5 | PLA is fine too<br/>:warning: Print a single build_helper_z and use it for all alignments |
| build_helper_y | 1 | 0.20 | 15 | 3 | 5 | PLA is fine too<br/>:warning: Print a single build_helper_y and use it for all alignments |
| y_end_caps | 2<br/>(total of 4 parts) | 0.20 | 20 | 4 | 5 | PLA is fine too |
| z_end_caps | 1<br/>(total of 2 parts) | 0.20 | 20 | 3 | 5 | PLA is fine too |
| foot | 4 | 0.20 | 20 | 3 | 5 | PLA is fine too |
| lcd_support_a | 1 | 0.20 | 20 | 3 | 5 | |
| lcd_support_b | 1 | 0.20 | 20 | 3 | 5 | |
| psu_lower_mount | 1 | 0.20 | 20 | 3 | 5 | same for black and silver versions |
| psu_upper_mount | 2 | 0.20 | 20 | 3 | 5 | same for black and silver versions |
| rambo_base_lower_mount | 1 | 0.20 | 20 | 3 | 5 | |
| rambo_base_upper_mount | 1 | 0.20 | 20 | 3 | 5 | |
| rambo_lid_lower_hinge  | 1 | 0.20 | 20 | 3 | 5 | |
| rambo_lid_upper_hinge  | 1 | 0.20 | 20 | 3 | 5 | |
| y_bearing_holder | 3 | 0.20 | 20 | 5 | 5 | |
| y_belt_holder | 1 | 0.20 | 20 | 4 | 5 | |
| y_idler_tensioner | 1 | 0.20 | 20 | 4 | 5 | |
| y_idler_mount | 1 | 0.20 | 20 | 4 | 5 | |
| y_rod_holder | 4 | 0.20 | 20 | 4 | 5 | |
| y_motor_mount | 1 | 0.20 | 20 | 4 | 5 | |
| y_motor_endstop_mount  | 1 | 0.20 | 20 | 4 | 5 | Only for MK2S or MK2.5(S) |
| z_leadscrew_cap | 2 | 0.20 | 20 | 2 | 5 | |
| z_motor_mounts | 1<br/>(total of 2 parts) | 0.20 | 20 | 4 | 5 | |
| z_tops | 1<br/>(total of 2 parts) | 0.20 | 20 | 4 | 5 | |
| cable_clip_horizontal  | 2 | 0.15 | 20 | 4 | 5 | |
| cable_clip_vertical | 6 | 0.15 | 20 | 4 | 5 | |
| cable_clip_lcd | 5 | 0.15 | 20 | 4 | 5 | |

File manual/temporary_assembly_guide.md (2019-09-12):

# Bear Upgrade 2.1

## Temporary assembly guide for new parts of Bear Upgrade 2.1

### Warning :warning:

Please refer to assembly guide for Bear Upgrade 2.0 for the complete assembly.

This is only covering temporarily the new features of Bear Upgrade 2.1.

:warning: Those instructions are for advanced users, if you are not sure how to proceed, please wait the final release.

### Y Axis

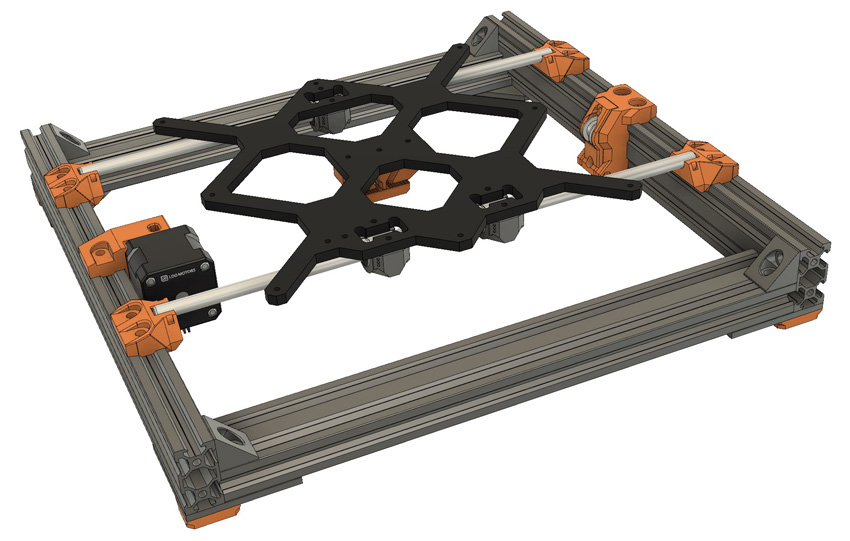
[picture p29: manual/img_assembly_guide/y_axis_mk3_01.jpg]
y axis mk3


#### Parts that needs to be printed

  1. y_idler_mount
  1. y_idler_tensioner
  1. y_belt_holder
  1. y_motor_mount
  1. y_motor_endstop_mount (MK2S, MK2.5(S) only)

#### Removing unused t-nuts

You will need to remove some t-nuts that are blocked by the black angle corner. Follow these instructions to remove them properly.

:bulb: Those are images from MK3 frame but use the same idea for Bear Upgrade MK2S, MK2.5 frame.

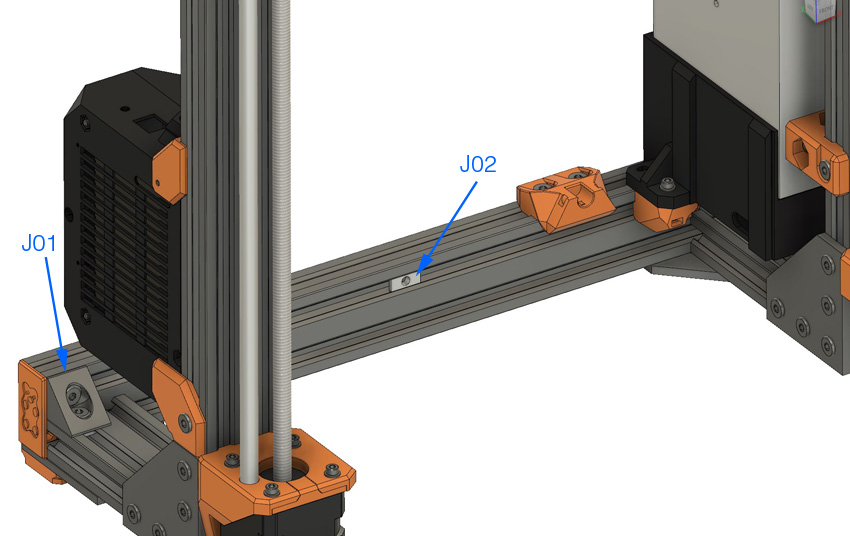
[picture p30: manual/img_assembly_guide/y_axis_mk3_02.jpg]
y axis mk3


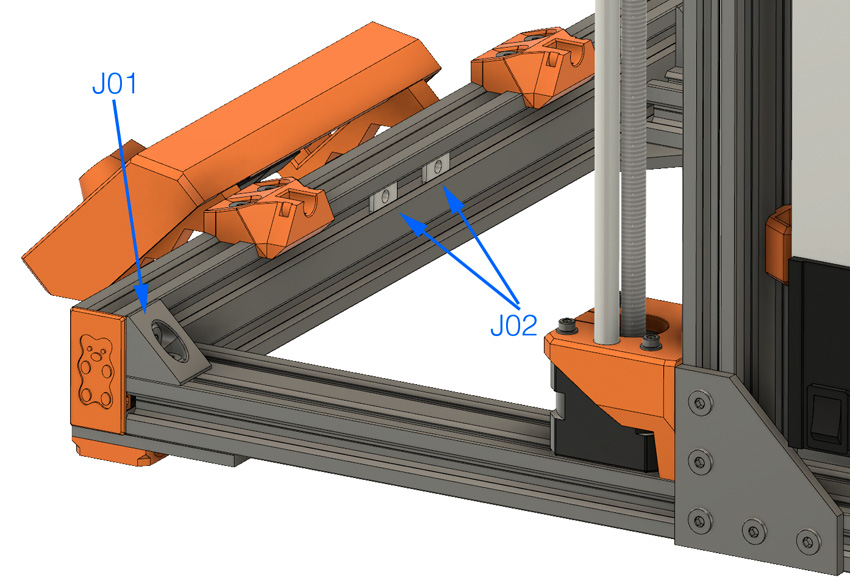
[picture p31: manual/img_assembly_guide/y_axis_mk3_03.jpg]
y axis mk3


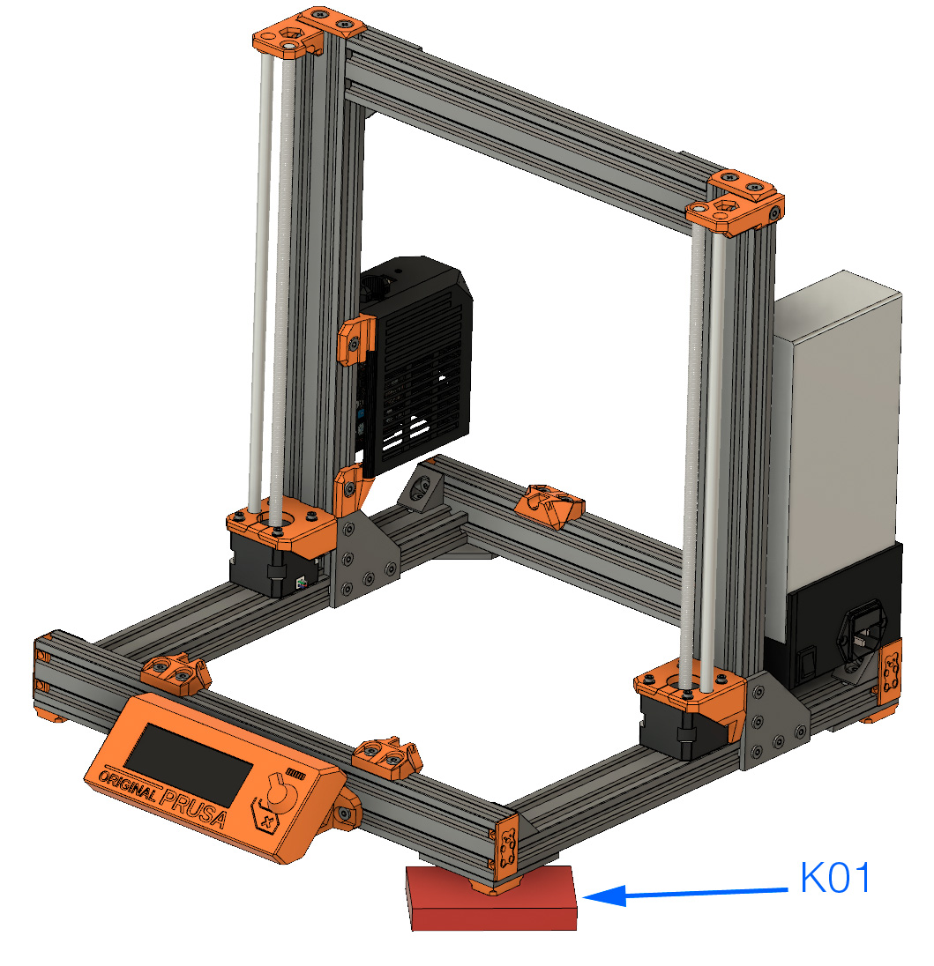
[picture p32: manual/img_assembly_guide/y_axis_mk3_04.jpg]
y axis mk3


  1. Remove the end caps.
  1. **J01:** Remove top screw and t-nut of one black angle corner on the Y idler or Y motor side.
  1. **J02:** Remove the t-nut(s) that are in the top row.
  1. **K01:** Retighten the black angle corner and verify the frame is still flat. If necessary, add something in the corner and press the frame on opposite corners to make it flat again.

#### Y Belt Holder

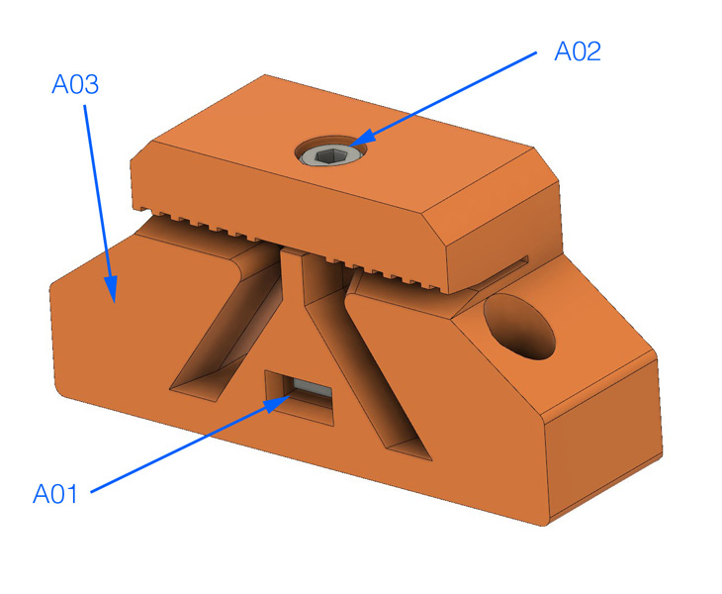
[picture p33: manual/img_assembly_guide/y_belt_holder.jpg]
y belt holder A

  * **A01:** M3 square nut
  * **A02:** M3x18mm
  * **A03:** This face must face the two bearings side of the Y carriage

Insert the belt and secure it with A02.

#### Y Idler

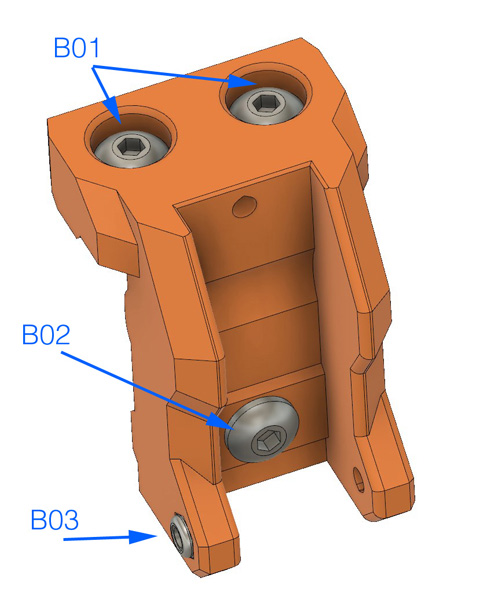
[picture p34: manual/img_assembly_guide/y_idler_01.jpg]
y idler B

* **B01:** M5x10mm
* **B02:** M5x10mm
* **B02:** M3 locknut

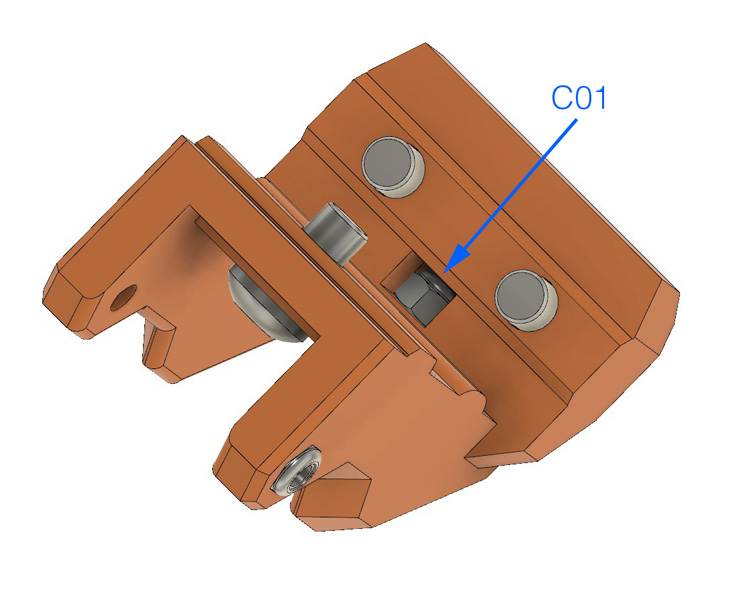
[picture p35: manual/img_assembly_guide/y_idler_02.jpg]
y idler C

* **C01:** M3 locknut

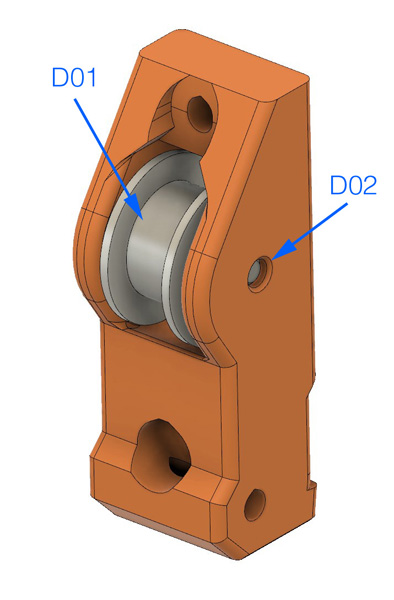
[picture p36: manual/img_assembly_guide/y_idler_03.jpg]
y idler D

* **D01:** Prusa 20T smooth idler
* **D02:** Dowel pin

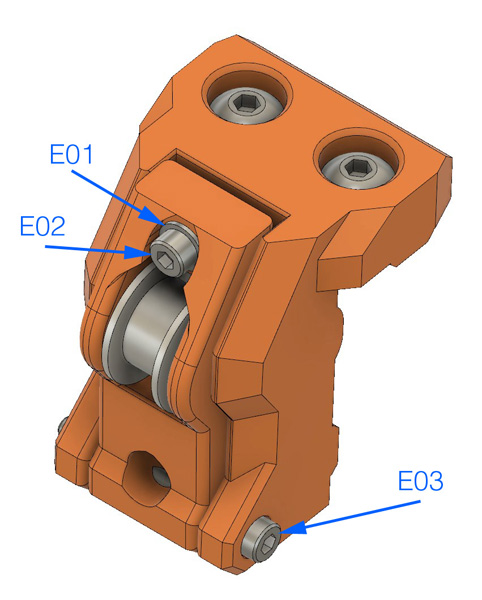
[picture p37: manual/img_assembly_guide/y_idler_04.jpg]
y idler E

* **E01:** M3 washer
* **E02:** M3x25mm
* **E03:** M3x30mm

Try to keep the tensioner as closed as possible. Move the belt by 1 or two teeth from the Y belt holder if necessary.

# Y Motor Mount MK2S, MK2.5(S)

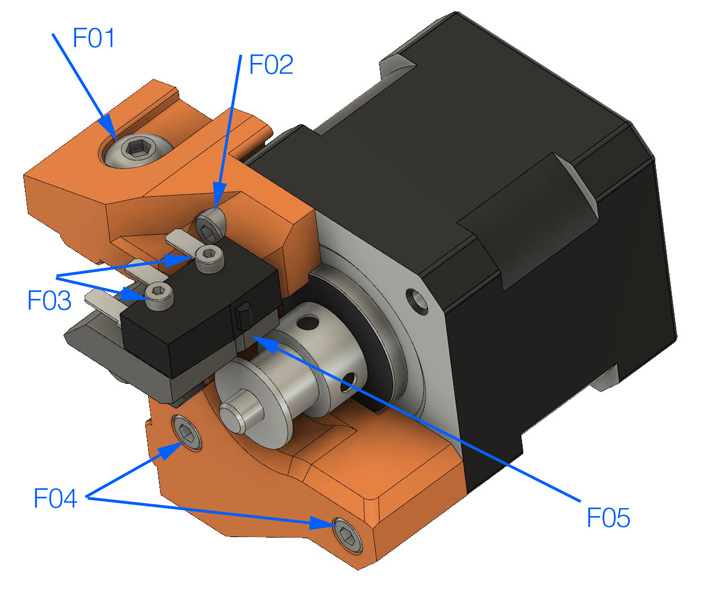
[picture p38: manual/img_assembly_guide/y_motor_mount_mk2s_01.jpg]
y motor mount mk2s F

* **F01:** M5x12mm
* **F02:** M3x10mm
* **F03:** M2x12mm
* **F04:** M3x18mm
* **F05:** Align the endstop pin with the slit

Press the motor in the direction of the vslot when tightening F02 and F04 screws.

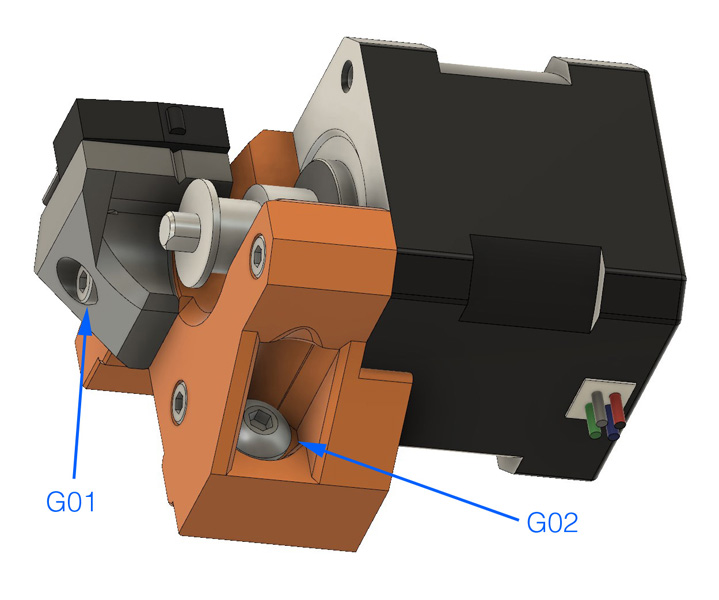
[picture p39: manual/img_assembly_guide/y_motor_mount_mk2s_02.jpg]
y motor mount mk2s G

* **G01:** M3x10mm
* **G02:** M5x16mm

# Y Motor Mount MK3(S)

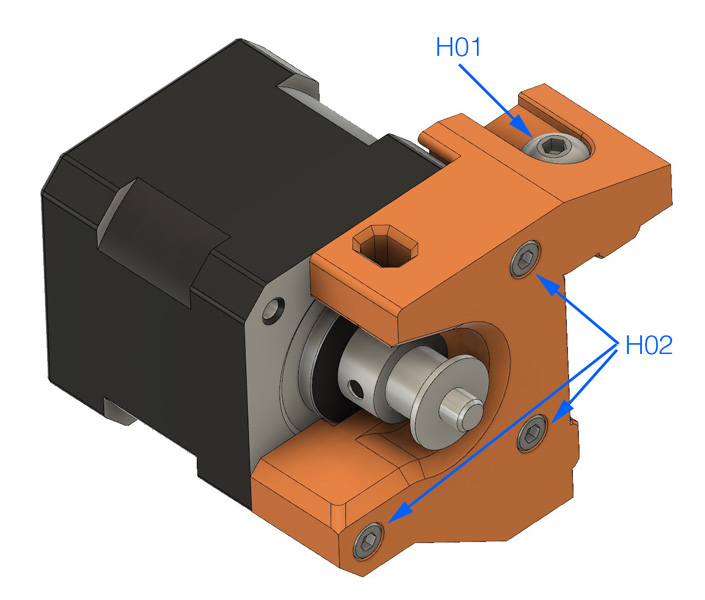
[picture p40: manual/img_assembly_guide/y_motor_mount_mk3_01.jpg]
y motor mount mk3 H

* **H01:** M5x12mm
* **H02:** M3x18mm

Press the motor in the direction of the vslot when tightening H02 screws.

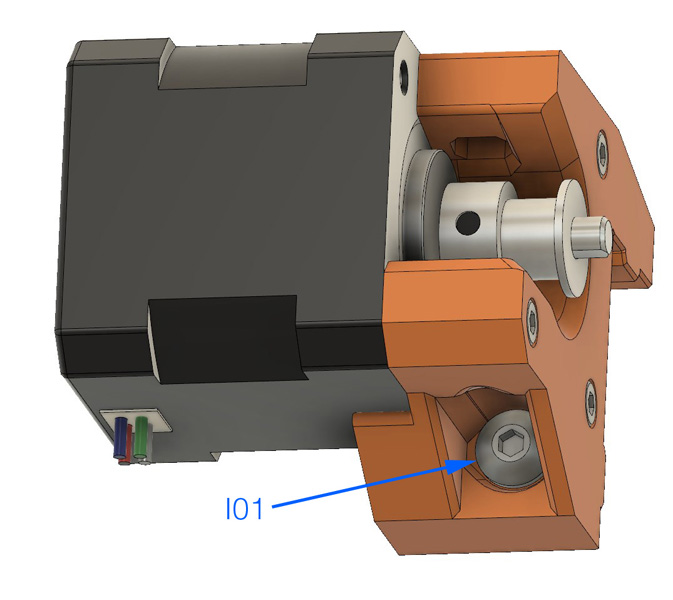
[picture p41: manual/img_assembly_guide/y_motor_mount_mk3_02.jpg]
y motor mount mk3 H

* **I01:** M5x16mm

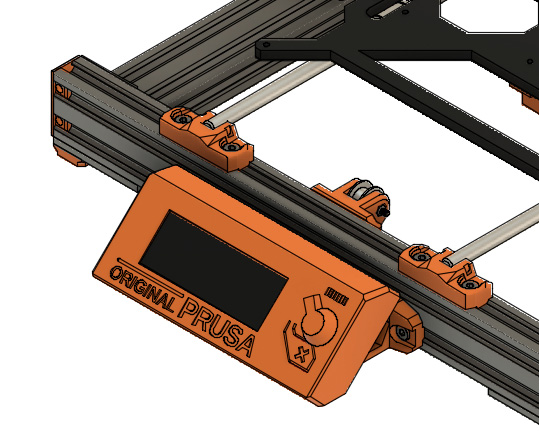
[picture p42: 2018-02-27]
full_upgrade/for_mk2.5/manual/assembly_instructions/img/fig14.3.jpg

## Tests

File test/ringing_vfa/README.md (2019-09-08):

# Ringing and VFA Test

## Test parameters

  * Material: PETG black
  * Speeds: 25, 50, 75 and 100 mm/s
  * Slicer: PrusaSlicer
  * Slicing parameters:
    * 0.4mm nozzle
    * 0.2mm layer height
    * 0.45mm extrusion width
    * Printing temperature needs to be adapted to speed (around 240°C to 260°C)
    * Spiral vase
    * No bottom layers
    * Brim only if bed adhesion is difficult
    * Must not hit cooling threshold (double check speed in gcode file directly)
    * Max volumetric speed: min 9mm^3/s
  * Printer parameters:
    * Bear MK3(S)
    * Extrusion multiplier calibrated
    * Temperature calibrated according to speed

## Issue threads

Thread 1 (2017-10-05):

measurements, Y axis

zagarolo, 2017-10-05:
Hi his beautiful compliment project continue and I'm here better with her !!

I bought all the prices for assembling the Y axis ...

I have some questions:

the original MK2S pria fit the 100mm Y axis instead of its 110mm V-Slot design and 185mm later, its 195mm V-Slot design ever? Bearing Y bearings may have length problems

excuse my English to use the translator

gregsaun, 2017-10-05:
Thank you so much for the compliments, this is really helping me!

On the original MK2(s) those measurements are done from top of the rod holder, not from of the rod hole. It is difficult to explain, hope you understand. You can also have a look on this drawin for the MK2 : https://raw.githubusercontent.com/PrusaMK2Users/MK2_Tips_and_Tricks/master/Prusa-i3-mk2-Dimensions.png

If you carefully check the rod holders, they are just a bit bigger than the 20mm (width of the vslot), this is to have the exact same dimensions as the MK2(s) (rod hole is 9.75 long and between front of the hole and front of the piece you have 9.50).

However, I did two different piece from back and front and that is wrong. I didn't remember why I did this and there is effectively an issue! Thanks for that, will fix it today :)

gregsaun, 2017-10-05:
So I remember why I did different front and back rod holders. This is due to the fact the frame is not 6mm thick but more 6.2-6.3mm on mine. So, on the original, you have 185 only if you have a frame that is 6mm, otherwise you will compensate the difference by screwing a bit more on the rod.

I will make all rod_holders similar and the difference will be compensated when screwing in the vslot.

gregsaun, 2017-10-05:
01bf8536e8f9c28e50426bd4b3f99f8dfb1a0566

Closed 2017-10-05.

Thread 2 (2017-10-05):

Interference with psu_lower_mount and latest PSU cover

gregsaun, 2017-10-05:
From Jeepguy42 on Thingiverse :
https://www.thingiverse.com/thing:2562174/#comment-1551150
http://www.openbuilds.com/threads/prusa-i3-bear-edition.10274/#post-58904

zagarolo, 2017-10-06:
hi thank you for your reply...

you add print setting is for all parts or only psu and holder mount ? thanks

zagarolo, 2017-10-06:
drill new holes print 3d for frame Z ?

gregsaun, 2017-10-07:
Zagarolo> I have created a new issue for your question, I would like to keep this issue clean and focused to the psu_lower_mount / psu cover only. Here is the new issue : #3

Closed 2017-10-07.

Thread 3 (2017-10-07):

Questions from Zagarolo

gregsaun, 2017-10-07:
> hi thank you for your reply...
>
> you add print setting is for all parts or only psu and holder mount ? thanks

> drill new holes print 3d for frame Z ?

gregsaun, 2017-10-07:
I am currently testing all prints and once I have the expected results I add it to the print settings. All pieces will be in as soon as I can ;)

I do not understand what you means by "drill new holes print 3d for frame Z ?"

zagarolo, 2017-10-07:
I have printed all the parts, should I print everything?

yes, holes for Z axis

Can a print be positioned above to help for the holes?

zagarolo, 2017-10-07:
sorry

Have I printed all the parts, should I reprint everything?

zagarolo, 2017-10-07:
wait for new settings to print?

gregsaun, 2017-10-08:
If your print settings are stronger than what I propose, then you do not necessarily need to reprint them. However, I am still working on each printed parts and solve details and sometime serious issues like the psu mounts. You might have issues when using the parts you have printed it. If that is the case, check if there is an update and if not you can raise a bug here.

Here are the dimensions for the Z axis holes :
https://github.com/gregsaun/prusa_i3_bear_upgrade/blob/master/doc/frame_drilling_dimensions.pdf

I have done a plate but never tested it, so use it with caution (and please report feedback) :
https://github.com/gregsaun/prusa_i3_bear_upgrade/blob/master/printed_parts/stl/drilling_helper.stl

zagarolo, 2017-10-08:
Hi

I read a comment where to ask for help to complete the list of the pieces as never are they all?

zagarolo, 2017-10-08:
I've already bought all the pieces ready to be cut

zagarolo, 2017-11-01:
Hi I mounted all the printer I inserted igus new bearings and rods the printer works but Z wobble even with the original rods and bearings, I confirm to modify psu mount 1 mm even if very fixed, another problem the rod clamps come in in the cart. the Zwobble same thing with the new Z tops you've designed in optional parts.
if you have an email I'll send you the photos

gregsaun, 2017-11-01:
Hi Zagarolo, it should not Z wobble, the only flex you can have might come from the alu frame. I got another feedback and it was clearly sturdier and no wobble.

I do not understand what do you mean by "another problem the rod clamps come in in the cart".

For the images, you can use image hosting services and use the following code in your comment :
```markdown
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
```

Did you use Openbuilds parts or other brands?

Some things to check :
* All screws
* Rods should not move in the rod_holders, it should be tight
* Threads made in the vslots to fix the frame
* Extruder calibration

zagarolo, 2017-11-01:
hi

All screws = yes ok
Rods should not move in the rod_holders, it should be tight = yes ok
Threads made in the vslots to fix the frame = yes ok
Extruder calibration = yes ok

problem zip fix rod asix X

zagarolo, 2017-11-01:
use Openbuilds parts

gregsaun, 2017-11-02:
Could you add pictures here?

Could you explain what do you mean by this two sentences :
*"problem zip fix rod asix X"*
*"another problem the rod clamps come in in the cart"*

gregsaun, 2017-11-02:
Is this issue what you are talking about?
https://github.com/gregsaun/prusa_i3_bear_upgrade/issues/8

gregsaun, 2017-11-06:
I close this one as we continue on the other one :)

Closed 2017-11-06.

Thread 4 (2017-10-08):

Sources for extrusion

FischOderAal, 2017-10-08:
I've seen that you plan to cut everything yourself. Sometimes this and openbuilds (due to taxes) is not an option, so maybe it makes sense to list options where you can order the pieces pre-cut. For Germany good sources are:
http://www.motedis.com
http://kritec-gmbh.de

gregsaun, 2017-10-08:
Good idea, we can start listing few here. Please, anyone know a good one, please help us to complete the list :)

UK : ooznest.co.uk (very good)
Portugal : http://www.ratrig.com (not tested)

FischOderAal, 2017-10-11:
Some more:
Germany: http://www.watterott.com/de/Mechanik/V-Slot-Profile
Germany: http://www.conucon.de/de/29-openbuilds
France: http://www.vslot-europe.com/home/8-vslot-rail.html
Switzerland: https://www.3dware.ch/OpenBuilds-V-Slot-Profil-20mm-x-40mm-x-1000mm-De.htm

I also found this:
https://www.google.com/maps/d/u/0/viewer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

That was all I could find while going through a mug of coffee :)

gregsaun, 2017-11-06:
Forget to say thank you FischOderAal, sorry! Thank you then :)

I have added a page with online shops selling official Openbuilds hardware (and pre-cut option) : https://github.com/gregsaun/prusa_i3_bear_upgrade/blob/master/doc/openbuilds_shop_list.md

DoItWithASmile, 2018-02-28:
This is more FYI:
I received my hardware from RatRig today. Here is something I really don't like with most shops listed:

The tee nuts are terrible!
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

This is how a proper tee nut should look like IMHO:
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

gregsaun, 2018-02-28:
They look like similar to Openbuilds tee nuts :
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

I totally agree they are not the best one but they work pretty well and they are cheaper than "bigger" ones.

DoItWithASmile, 2018-02-28:
Found a shop in Algeria offering v-slot heavy duty nuts for 0.10 EUR per piece 😅
www.dzduino.store

No pre-cutting of extrusions though.

gregsaun, 2018-03-01:
I did not realize yesterday but those type of tee nuts will enter in contact with my printed parts due to the extra material on top

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

However this type will be good (from dzduino.store) :
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

dukemagus, 2018-03-01:
https://www.tdtec.com.br/

These guys sell 20x40 aluminum profiles on the openbuilds.com format in Brazil.

You'll need to contact them to be sure of which other related components they sell, though

gregsaun, 2018-03-01:
Thank you, I have added them to the list. tdtec.com.br does not work in my country, are you sure about the link?

Panayiotis-git, 2018-03-01:
Greece: https://grobotronics.com/mechanics-and-wheels/openbuilds-v-slot/

gregsaun, 2018-03-01:
Thanks!

adam6666, 2018-03-03:
India - https://www.3dprintronics.com/Aluminium-Extrusions-c7124102 . They have V Slot extrusions and accessories but are not official V Slot distributors.

fishmsk, 2018-03-04:
Russia - https://soberizavod.ru/
They have aluminum extrusions, screws, tee nuts, plates etc. The only difference from Openbuilds' extrusions is a hole - it is for M6 thread here (Openbuilds ones have holes for M5 thread).

gregsaun, 2018-03-04:
Thank you all, we start to have a nice list :)

fishmsk > Do you mean the tee nuts are M6? Do they propose cutting service?

adam6666, 2018-03-04:
https://www.3dprintronics.com/Aluminium-Extrusions-c7124102 these guys provide precise customized lengths of all the T slots and V Slots.

fishmsk, 2018-03-05:
gregsaun -> Yes, they provide cutting service.
I mean not Tee nuts hole but the hole in the extrusion itself. Please see the drawings below:
[http://protein.nmr.ru/fish/pics/soberizavod_vs_openbuilds.jpg](url)

gregsaun, 2018-03-05:
Thanks  adam6666 and fishmsk.

I have just added new stores in Canada, Norway, Spain and Sweden.

DoItWithASmile, 2018-03-15:
Denmark: https://3dnielsen.dk

Didn't check if they offer pre-cut.

DoItWithASmile, 2018-03-15:
They to offer pre cut with +/- 0.5 mm

gregsaun, 2018-03-15:
Thank you, it's in  :)

adam6666, 2018-03-21:
Hello Greg
There is a slight issue which I am facing. My printer is complete but during calibration, it shows left front calibration point can't be reached. Although when I check it manually, the pinda probe is exactly in the center of it. Please advise

gregsaun, 2018-03-21:
Hi adam, I have opened a new issue here : https://github.com/gregsaun/prusa_i3_bear_upgrade/issues/20

jhoff80, 2018-04-06:
Will the RatRig kits still need the joining plates to be filed down slightly?  I assume so, but just wanted to check before buying a tool for that.

gregsaun, 2018-04-06:
That is a good question because they are coming in black! No one report something about this and I do not have RatRig plates in hand so hard to give an precise answer. I will ask RatRig directly and come back to you ;)

gregsaun, 2018-04-09:
Got an answer from RatRig, plates are not sharp like original Openbuilds plates so no need to file them. I'll add a note in the manual. Thanks for reporting :-)

kberck, 2018-07-11:
Does the extruded aluminum have to be v-slot specifically?  I have some t-slot available, but it doesn't have the chamfered edge of the v-slot.  Wanted to check before I start cutting so I don't hit a roadblock later on.
Thanks!

gregsaun, 2018-07-12:
@kberck yep this is mandatory because of the way my parts are designed. Also check here :
https://github.com/gregsaun/prusa_i3_bear_upgrade/issues/39

martinkaersgaard98, 2019-02-02:
To the list of sources of V-slot rail and other OpenBuilds parts you can add Danish shop: makersupplies.dk

sparkyman215, 2019-04-26:
The NA - Texas distributor: smw3d tries to redirect to hobby-fab.com, a parked website. Suggest removing from list

gregsaun, 2019-04-30:
@sparkyman215 thanks!

Closed 2019-11-07.

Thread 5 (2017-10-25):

Having troubles with frame_drilling_dimensions.pdf

alomex21, 2017-10-25:
I printed with adobe acrobat reader with real size, which print the size of the paper (letter in my case) intead of the whole sketch, as the result of some of the distances doubled(center of the aluminum extrusion with the edge of the z frame, which measures 120mm instead of 60mm and 40 mm instead of 20mm). Any help on this?
Thanks
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

FischOderAal, 2017-10-25:
In the end, it is only a sketch. I guess it was scaled to emphasis the details. You should print the drill template.

gregsaun, 2017-10-25:
I think you are both right :)

I made this drawing on A3 paper, this could explain why it is 2 times bigger. Be careful when using the printed design, carefully check all dimensions.

gregsaun, 2017-10-25:
For your information, the problem is that I used a scale of 2:1 to make this drawing. I have fix it by adding the scale on the drawing. You should then print 2x smaller.

Thanks for your feedback  :)

Closed 2017-10-25.

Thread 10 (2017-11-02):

Thanks gregsaun

zagarolo, 2017-11-02:
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

gregsaun, 2017-11-02:
:heart_eyes:

So good to see this in real!

y_rod_holder will be fixed in priority

zagarolo, 2017-11-02:
look at my side printing to see it's a bit misaligned or Z wobling you have a tip

gregsaun, 2017-11-02:
Did you re-calibrate the printer (calibrate xyz)? Did you check your Z level again?

zagarolo, 2017-11-02:
yes, lined XYZ I did not re-align Z axis again

gregsaun, 2017-11-02:
This might comes from the y_rod_holder too. Let's fix this first.

zagarolo, 2017-11-02:
Ok

FischOderAal, 2017-11-02:
This looks great. Congrats!

zagarolo, 2017-11-02:
Thanks

gregsaun, 2017-11-03:
New rod_holder available :)

zagarolo, 2017-11-05:
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

gregsaun, 2017-11-05:
yip yip :)

Do you speak Italian? I understand a little bit so you can write in italian and I will answer in english. (my mother tongue is french and I understand a very little bit of german as well)

zagarolo, 2017-11-05:
Ciao si sono italiano

zagarolo, 2017-11-05:
Ho visto che hai modificato rod holder oggi stampare e proverò

gregsaun, 2017-11-05:
I have seen the "quasar vetri" in your picture ;)

Nice. Do you have another spool of orange? :grin:

zagarolo, 2017-11-05:
Siii bello ho finito ultima bobbina ,,😯😩

zagarolo, 2017-11-05:
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
E finita 😰😰😰😭😭😭😭

gregsaun, 2017-11-05:
In case of I am using MF-PETG Neon Orange from extrudr.eu which is very very close to Prusa orange.
https://extrudr.eu/collections/petg/products/extrudr-mf-petg-neon-orange

zagarolo, 2017-11-05:
Si Colere molto vicino a Prusa

gregsaun, 2017-11-05:
I have added feet. For now, they have same shape than MK2(s), like this you can reuse your (home made) dampers

gregsaun, 2017-11-09:
I finished first build yesterday, the black corner on aluminum plate very makes the build very hard to square/tight. After several test on how we can square them correctly I have decided to remove them. Did you use them?

zagarolo, 2017-11-09:
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

zagarolo, 2017-11-09:
ciao ordinato  MF-PETG Neon Orange  e stampato tutto cosa ti riferisci black corner on aluminum plate yes

come nel tuo progetto la parte del motore installati in basso e la parte anteriore cioe lcd  installati in alto per non avere problemi con il carrello si bloccava

zagarolo, 2017-11-09:
Hello ordered MF-PETG Neon Orange and printed everything you say black corner on aluminum plate yes

as in your project the part of the engine installed at the bottom and the front ie lcd installed up to not have problems with the car locked

gregsaun, 2017-11-09:
Ok thank you, I will still remove them, easier and cheaper and does not impact rigidity.

For MF-PETG Neon Orange I print at 225°C and 80°C for bed. Fan I am still testing but at 30-50 for now...

zagarolo, 2017-11-09:
MF-PETG 240  for bed 90 is perfect linear

zagarolo, 2017-11-09:
Manufacturer datasheet is 240 bed 90

gregsaun, 2017-11-09:
Where did you get the datasheet, on their website is 205 and 80? https://extrudr.eu/collections/petg/products/extrudr-mf-petg-neon-orange

zagarolo, 2017-11-09:
https://www.3djake.it/extrudr/filamento-mf-petg-neon-arancione

zagarolo, 2017-11-09:
Cosa sono queste righe più grande durante la stampa ? I puoi aiutare
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

zagarolo, 2017-11-09:
ABS
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

gregsaun, 2017-11-09:
Thanks for the link, interesting!

This is due to the fact it is doing parts of the line, then go somewhere else and then finish the started ones. Then you have this joining line. I do not know how to solve it but some things you can check :
- layer height
- extruder calibration (over extrusion?)
- extruder temp?

zagarolo, 2017-11-17:
All parts orange neon petg
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

gregsaun, 2017-11-17:
Sweet build! In case of I updated the lcd supports to avoid colliding to with rod holders.

Do you still have the wobbling from the previous version?

zagarolo, 2017-11-17:
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
Hello no wobbling

zagarolo, 2017-11-17:
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

gregsaun, 2017-11-17:
Cool! Do you find it sturdier? Do you see a difference in print quality?

zagarolo, 2017-11-17:
si molta differenza no wobbling qualità superiore

zagarolo, 2017-11-17:
ci sono un po di peli

gregsaun, 2017-11-17:
This is due to the filament, you can remove them using a hair gun :
https://www.youtube.com/watch?v=uqUcrIsSHak
You can also play with retraction but I never tried

gregsaun, 2017-11-17:
You can try to reduce temp a bit as well, I am at 225°C

zagarolo, 2017-11-17:
print 205

zagarolo, 2017-11-18:
Hi problem wobbling
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

gregsaun, 2017-11-19:
It does not look to be a wobbling issue to me.

* If the part is brittle, then you should increase temp and print slower
* Clogged nozzle?
* Does the temperature variate during the print?
* Filament is getting stock or tangled

zagarolo, 2017-11-21:
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

https://github.com/prusa3d/Prusa-Firmware/issues/75#issuecomment-311386115

Sebastianv650/Prusa-Firmware/tree/MK2_Community_Mod

Very very good

gregsaun, 2017-11-21:
So good, I have to update my firmware!

zagarolo, 2017-11-21:
https://github.com/prusa3d/Prusa-Firmware/releases/tag/v3.1.0-RC2

Read

zagarolo, 2017-11-21:
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

gregsaun, 2017-11-21:
Yep I read it and just finished to upgrade my firmware, let's go to calibrate the K value! Very nice new feature!

zagarolo, 2017-11-21:
Is very very faster print

zagarolo, 2017-11-25:
Ciao mi servirebbe se possibile un grande favore non sono capace a disegnare e creare un file stl per ABS  e Mi servirebbe urgentemente una modifica sul file originale Prusa mk2s asse X end e motor adatti per cuscinetti igus 15 mm ho un grande problema ti allego la foto grazie
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

gregsaun, 2017-11-25:
Could you describe your problem?

zagarolo, 2017-11-25:
Guarda la foto il cuscinetto si muove scende nella parte interna

Look at the photo the bearing moves down to the inside

zagarolo, 2017-11-25:
create file in abs and petg

zagarolo, 2017-11-25:
I would be very grateful if you could create the abs file and pet parts original X end axis, and the engine part

gregsaun, 2017-11-26:
I do not thing it is a big deal if the bearing are going a bit inside. For now I do not have lots of time, I would like to finish the bear upgrade first to start a new one.

What you can simply do is this :
- Download MK2s scad files from here https://www.prusa3d.com/prusa-i3-printable-parts/
- Install OpenScad
- Open bearing.scad and reduce bearing_diameter value by 0.1 o 0.05mm (top of the file) and save
- Open x-end-idler.scad, then hit F6, then File -> Export -> STL
- Open x-end-motor.scad, then hit F6, then File -> Export -> STL

zagarolo, 2017-11-26:
New project ?

zagarolo, 2017-11-26:
Vorrei investire sto cercando di fare qualcosa di grosso cerco persone per investire denaro in nuovi progetti aprire una fabbrica io sono un costruttore di case ma ho sempre fatto elettronica vorrei investire miei soldi in qualcosa di grande

zagarolo, 2017-11-26:
Spero che il tuo nuovo progetto usare componenti di alta qualità e tecnica superiore per pezzi

zagarolo, 2017-11-26:
Quanti anni hai ?

gregsaun, 2017-11-26:
Could you contact via my website here : https://www.ekunn.com/ -> contact

zagarolo, 2017-12-02:
help I have a height problem of carriage Y extruder slams in the pot how can I change the end of the stroke find the new zero point? I modified bearings with double bearing under the carriage Y but increased height thanks

zagarolo, 2017-12-02:
appassionato di droni ?

zagarolo, 2017-12-02:
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
Mio drone DJI Spark modified firmware adesso può andare a 2 km o 4 km

Closed 2017-12-19.

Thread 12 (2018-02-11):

Extrusion lengths

coreykovacs, 2018-02-11:
In this drawing

https://github.com/gregsaun/prusa_i3_bear_upgrade/blob/dev/full_upgrade/for_mk3/doc/vslots_length.png

It has the side uprights at 334 mm, but doesn't appear to take into account the fact the bottom side extrusions are laying flat in the V2 model. Shouldn't they then be 354mm ?

gregsaun, 2018-02-12:
You are totally right. BOM has the correct length. Thanks :)

gregsaun, 2018-02-13:
fixed

coreykovacs, 2018-02-13:
Sorry to be a nag. I see you corrected the measurements on the side but the measurements in the center of the drawing are still wrong and say the Z parts are 334 instead of 354. Looks awesome though and I can't wait to build one.

gregsaun, 2018-02-13:
Damned! Thanks for your patience :bowtie: . Those heights will be increase soon (another bug found during the first build).

I do not have a MK3 (waiting my 2.5 upgrade), so would be nice to have someone that would like to try the adventure!

coreykovacs, 2018-02-13:
it's no problem at all and I'm glad to be of help in any way.

gregsaun, 2018-02-15:
Thank you for your help. I have updated the files for Half upgrade and Full Upgrade MK2(s) and MK2.5. I still have to work on MK3 (Z will be just a bit higher).

Note that I also removed the unused PDF except for drilling the Half Upgrade frame (some builder like to print it and double check the holes positions).

Closed 2018-02-20.

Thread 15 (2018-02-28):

MK3 Full: Y-Motor mount different between STL and assembly instructions

DoItWithASmile, 2018-02-28:
I noticed an issues in the MK3 assembly instructions with regards to the y-motor mount:
Step 3.2: 2x tee nuts are inserted in the same slot. Later on the y-motor will be installed here, see step 8.2
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

However, the y-motor mount in the STL uses two nuts in two slots on the same side:
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

Option 1: instructions are outdated
- add 3rd tee nut
- modify fig 8.2 to depict current mount

Option 2: mount is outdated
- update STL

gregsaun, 2018-02-28:
That was the STL like in issue #16. I close this one as it as been fixed now. Thanks for reporting this.

Closed 2018-02-28.

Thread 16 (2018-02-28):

MK3 Full: Y-Mount different from MK2(.5s)

DoItWithASmile, 2018-02-28:
The y-motor mount of the MK3 is different to the MK2s in one important way:
the MK2s mount uses 3 screws to fix the motor, the MK3 mount only uses 2. Is this intentional?

MK2s:
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

MK3:
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

Since both mounts are for NEMA 17, the holes should be same.

BTW: The after market EINSY board can be bought with an endstop! so even though Prusa Research does not ship the MK3 with one, it would not be a problem to reuse the MK2s mount design with endstop.

gregsaun, 2018-02-28:
This is a bug, it is like my MK3 part is an older one, it should have 3 screws. BTW, original MK3 has only two

gregsaun, 2018-02-28:
I have exported the last version, that was an export issue. I keep this issue open until I have double check all exports. Thanks for reporting this :wink:

DoItWithASmile, 2018-02-28:
I know the original MK3 version only has 2. However, in the forum there were different beefed up designs:
- 3 screws to the backplate (included drilling holes... with the V-slot we can do this way easier)
- 3 screws to the stepper motor
- and even one where the stepper motor was held from both sides (that is what I printed: the y-mount from the STLs and a mirrored version for the other side of the motor. Quick and dirty. 😈)

gregsaun, 2018-02-28:
Yes you are right, I really do not understand the design of the original mount. Only two screws to mount the motor plus the arm are thinner than MK2s design...

I do not know the third design, do you have a link?

BTW, really sorry for this mistake, you will need to print one more, I hope you have enough filament...

DoItWithASmile, 2018-02-28:
I can confirm the newly exported STL looks like the assembly instructions.
Will print those with the next batch. New spool of filament arrived today. I am safe. 😃

Link to design no. 3: Prusa forum, ["Fine tune your MK3 Y axis"](https://shop.prusa3d.com/forum/original-prusa-i3-mk3-f30/fine-tune-your-mk3-y-axis-t13851-s20.html#p63825), rendering from RHD
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

DoItWithASmile, 2018-02-28:
I guess so. Couldn't find specs on the screws though. I guess I have to unscrew one to measure it...
Might check tomorrow since the printer is running.

Panayiotis-git, 2018-03-01:
If you intent to remove the screws from the back of the motor, be careful not to remove the rotor from the motor. It could result in a dramatic loss of motor torque at some steppers.

DoItWithASmile, 2018-03-01:
Good point. I just removed one. It's a M3 x 30 mm.

Closed 2018-03-01.

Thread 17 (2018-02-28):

End caps on z-axis missing?

DoItWithASmile, 2018-02-28:
The extrusion of the z-axis is not covered by end caps.
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

Suggestion: add a pair of end caps
- BOM: Add 1x pair of end caps, add 4x set screws
- add instructions to step 12 (at least for MK3)

gregsaun, 2018-02-28:
Yes I did not design them, they have to be a bit different than the one with the bear. I was hesitating between:

- 3d printed one with set screws mount
- 3d printed one with self tapping screws on top
- Openbuilds end caps http://openbuildspartstore.com/end-cap/

What do you think?

DoItWithASmile, 2018-02-28:
To stay true to the Bear Upgrade, here is my current thinking:

1. use 3D printed ones with set screws
2. why not ever so slightly modify the end caps we have:
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

This should fit here
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

gregsaun, 2018-02-28:
The problem are vibrations, this is why I have decided to use set screws and not only something that "clip" inside. Those "feet" for set screws are quite fragile and it is not really possible to make them stronger. So I like to keep the third "foot" in case one break or if you would to add one more screw.

I think I will purchase some self tapping screws for testing a first

DoItWithASmile, 2018-02-28:
In your experience did one ever break off due to vibrations?

Even a Bear Upgrade will be suspect to vibrations. That's for sure.
However, end caps are not load bearing. And wonder how and why they would break. 🤔

gregsaun, 2018-02-28:
I was not clear sorry, this is not a problem of breaking due to vibration, but the noise they can make if there are vibrating (because not correctly maintained).

Yes for sure Bear Upgrade will vibrate. Or it means you are not printing faster enough :grin:

Closed 2018-03-25.

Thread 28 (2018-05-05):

Documentation for V-Slot tolerances

gregsaun, 2018-05-05:

gregsaun, 2018-05-09:
Document has been send to Openbuilds for approval

gregsaun, 2018-05-24:
The drawing bellow (unit in mm) shows the impact of a cut that is a bit bigger on one side than the other. The difference used is the thickness of a hair (70um)!!! I used the longest vslot of the build as reference (which is only 360mm).

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

Imagine that if we have two vslots with this error and you put them in opposite direction, you will double the difference! You can also have an angle in XY plane, not only X or Y.

My (current) conclusion is :
1. Using plates to join extrusions solve the problem (compared to "Misumi style" with holes through extrusion)
2. Even with a perfect 90.000° cut you can have a small dust that will screw by a lot an axis
3. Assembly instructions might become more important than a perfect cut
4. This might explain why nobody is giving tolerance on the angle (even Misumi)
5. Software calibration of Z axis might be a good idea
6. The square used during the build needs to be very accurate and not too small

I have then decided to not add a tolerance on an angle in this document

gregsaun, 2018-05-24:
Document is available here :
https://github.com/gregsaun/prusa_i3_bear_upgrade/blob/master/doc/vslot_specs_tolerances_0.2.pdf

Closed 2018-05-24.

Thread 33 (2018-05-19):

Y belt tensioner

gregsaun, 2018-05-19:
Add a belt tensioner for Y axis

gregsaun, 2019-03-13:
That is very interesting, thank you. I am still not sure I like the tensionning but I think I will give a try to your way.

wavexx, 2019-03-13:
After using this for a while, I can say I wished I had control over the tilt of the X idler as well. I can now track the belt perfectly on the Y to the point that I re-aligned the belt path with a calipher (moving motor and idler in line with the carriage), and *then* adjusted the axis until the belt tracks in the center.

Sadly I cannot get the same perfection on the X. Due to the way the nylock bolt holds the X idler, going off there is pretty easy even if the part is printed correctly. I'm trying to think of a way to allow at least one end of the idler to be aligned with a screw, but there's not a lot of space to play with :/

gregsaun, 2019-08-21:
This is now fixed with the new release https://github.com/gregsaun/prusa_i3_bear_upgrade/releases/tag/2.1.0-alpha0.

Closed 2019-08-21.

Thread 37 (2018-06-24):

[Full MK3] Z Motor mounts are missing material

danclarke, 2018-06-24:
On the MK3 the standard mounting is with M3x10mm bolts rather than 12mm, and no washers. This means while the rear of the motor makes good contact with the mount, the front furthest from the aluminium extrusions is far from flush.

petethepig, 2018-06-26:
Yeah, I was also confused about that when I was looking through all the 3d printed parts.

There's this extra part called [z_motor_mount_front.stl](https://github.com/gregsaun/prusa_i3_bear_upgrade/blob/master/full_upgrade/for_mk3/printed_parts/stl/z_motor_mount_front.stl). Here's [the page from the assembly manual](https://github.com/gregsaun/prusa_i3_bear_upgrade/blob/master/full_upgrade/for_mk3/manual/assembly_instructions/step12.md).

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

danclarke, 2018-06-26:
Oh that's excellent, glad it was my mistake. I think I'll make a small PR to amend the docs in a few places. They're already very good, but a slight clarification here and there I think will make them even better for complete novices like myself.

Closed 2018-06-26.

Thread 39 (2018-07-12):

Use of regular 2020 T-Slot extrusions possible?

Drachenkaetzchen, 2018-07-12:
I have quite many 2020 T-Slot extrusions left over from a previous build. From the documentation it is not clear to me if V-Slot is really required, or if I can use regular T-Slot extrusions?

I know that the build uses 4020 extrusions, but if V-Slot is not really required, I'd give it a shot with 2020 T-Slot extrusions and share my experience.

Drachenkaetzchen, 2018-07-12:
To answer my own question: The V-Slot is required because the 3D-printed parts are designed that way.

I will see if I can modify them to fit regular T-Slot extrusions.

gregsaun, 2018-07-12:
Hi Drachenkaetzchen , sorry for my late answer...

Yes parts are design for v-slot. However, if you open the source file on F360 you will find parameters to set width and height of the tabs. Angle cannot be changed for now.

Also check this remix here : https://www.thingiverse.com/thing:2872569

Here are some reason why I use v-slot (not ordered) :
- V shape gives the ability to make accurate vertical alignment tabs like on this part : [rod holder](https://github.com/gregsaun/prusa_i3_bear_upgrade/blob/master/full_upgrade/for_mk2_mk2s/printed_parts/stl/rod_holder.stl). Thanks to this, almost no need to use a square to check alignment of printed parts. With t-slot you will need support and it comes with inaccuracy...
- Opensource with good community, FairShare program and regular contests with very good price
- Available in Europe and almost worldwide (Misumi is not available in Europe for private customers)! I know you can get T-slots from other places but they does not have the same profiles...
- 90° aluminum plates gives the perfect way to square the frame, even if cut is bad or dust is going in between. Plus 90° plates are very rigid! Check this drawing to see what is the effect of the thickness of a hair on a side of the extrusion : [effect of angled v-slot](https://github.com/gregsaun/prusa_i3_bear_upgrade/blob/master/doc/effect_of_angled_cut.jpg)
- V-slot can be used as linear rails (will come on the Bear after my extruder rework)
- Openbuilds offers a complete set of hardware build around v-slot made for automated machines

Drachenkaetzchen, 2018-07-12:
No need to be sorry - I appreciate your feedback and it's not late at all!

My motivation to use my existing 2020 extrusions is mainly because I'm on a budget, and I really want to get rid of the threaded M8 rods (like seen here: https://upload.wikimedia.org/wikipedia/commons/thumb/6/6a/Prusa_i3_with_metal_frame.jpg/800px-Prusa_i3_with_metal_frame.jpg ) - which is pretty awful for alignment anyways.

Also, from a quick look at #4 it seems there are no distributors in Germany where I could order them pre-cut. If I can relatively easily modify the Fusion360 sources to match my extrusions, I'll give it a shot.

Also, because my other 3D printer (MendelMax2 with heavy backlash issues) I couldn't guarantee that the printed parts are perfectly aligned, so I have to check everything manually as well.

Drachenkaetzchen, 2018-07-12:
Yes I've seen the store list, but well money is really an issue for me, so I try to use the existing parts which I have in stock. The link to the Thingiverse remix is pretty neat. You can close the issue if you wish. I might post it to this issue if I completed the build :)

gregsaun, 2018-07-12:
feedback is always welcome :-)
All doc is here : https://github.com/gregsaun/prusa_i3_bear_upgrade/tree/master/full_upgrade/for_mk2_mk2s/manual

Happy building!

fdjean, 2018-07-13:
@Drachenkaetzchen
I bought my aluminum bars at [Modetis.com](https://www.motedis.com/shop/) in Germany (I-Typ Nut 5).
I have the STL for the half upgrade if you need

Drachenkaetzchen, 2018-07-13:
@fdjean that would be awesome! Do you have them available to download somewhere (ThingiVerse?)?

fdjean, 2018-07-13:
@Drachenkaetzchen In my fusion360 storage  ;) I'll publish on thingiverse when I'm back home

gregsaun, 2018-07-13:
@fdjean thank you for sharing it :-)

Closed 2018-07-12.

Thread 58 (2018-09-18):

Step 15 of manual for 2.5 full upgrade.  M3 nut is called a bolt.

Tarpon907, 2018-09-18:
In the parts list:
1x M3 bolt (from the original PSU lower mount)

and in in assembly steps:
Add M3 bolt into the psu_lower_mount (figure 15.3)

Figure 15.3 correctly calls it a nut.

gregsaun, 2018-09-18:
Thanks :-)

Closed 2018-09-18.

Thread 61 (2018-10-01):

V-Slot parts and screws

DEvil0000, 2018-10-01:
With this build you need a lot of different none standard length v-slots. (You can buy them here in 5cm steps pre cut). It would be nice to have more of them the same length and in 5cm steps of length e.g. 350mm instead of 331mm.
For the screws its quite the same. Try to use the same legth everywhere and standard length like 10mm/16mm/20mm (8mm and 12mm are also fine but are normally not included in a set - here).
Additionally tee nuts are not a good choice.
It would be handy to have a step file combining all the parts as a overview.
I did quite the same as your full upgrade with my own design with standard v-slot length and only 20x20. Your design is better in a lot of ways but you need to cut the v-slots to quite some strange sizes.

matthew-humphrey, 2018-10-02:
I think the lengths were chosen so that the original Prusa parts would fit and provide an identical build volume. A big goal of this project is compatibility with the original (unmodified) printer.

gregsaun, 2018-10-03:
@DEvil0000 thanks for reporting this. I am interested to know where are you buying your v-slot? Do you have a link about your printer?

As Matt explained, one of the main goal is to propose a simple upgrade for Prusa printer, so I have to follow some dimensions. I agree with you that more "standard" lengths would be easier to manage for home made builds. I am planing to improve this on the next version, but I am not sure I can achieve it (specially on the Y axis). I prefer to have properly managed tolerances and strong printed part than standard vslot lengths.

8mm screws are what works best with Openbuilds plates so I will not change that one. 15mm will be updated to 16mm on the next version as it is not a standard length. I will have a look if I can switch the 12mm length to 16 or 10mmm, that is a good idea.

Could you tell me more about the tee nuts? What is wrong?

Good idea for the view of all parts!

DEvil0000, 2018-10-04:
The parts in this [repo](https://github.com/DEvil0000/Original-Prusa-i3/tree/MK3.5) are what I am using but maybe not 100% complete.
I am located in germany and was buying my v-slot at amazon (you find it when you search for e.g. ["Aluminium 20x20 150mm"](https://www.amazon.de/gp/product/B00K87LURW/ref=oh_aui_search_detailpage?ie=UTF8&psc=1) or "Aluminiumprofil 20x20 150mm"). There are at least 3 traders at amazon selling it: qfix robotics (where i got most of mine from), 3Diix and Dold Mechatronik (at their [items](https://www.amazon.de/Aluminiumprofil-20x20-I-Typ-Nut-50mm-2000mm/dp/B07D7BMG11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) site you can choose every 1cm). [qfix robotics](http://www.qfix.de/) also have a [webshop](http://www.qfixshop.de/) which is not working at the moment.
I know [Watterott](https://www.watterott.com/de/Mechanik/V-Slot-Profile) is also selling them which was the favourite shop at my university.
I had best results with those [nuts](https://i.ebayimg.com/images/g/VhoAAOSwMVdYGu91/s-l1600.jpg) - they give a strong and aligned hold.

gregsaun, 2018-10-04:
I agree that those nuts are better but I prefer to not have their extra tab in the middle and put this extra tab on plastic parts. This makes plastic parts stronger (and a low quality metal tee nuts will be still stronger than plastic).

Thanks for the store links, looks like you are using T-Slot mostly and not V-Slot (except if you are getting them from Watterott). I like vslot because you can print alignment tab vertically (you will need to use a support for t-slot and it is not reliable), plus it is open source with a useful community. In case it might be useful, have a look to the Openbuilds store list here : https://github.com/gregsaun/prusa_i3_bear_upgrade/blob/master/doc/openbuilds_stores_list.md

If you like you can fork my project (it is under GPL because I have to use the same license than Prusa, so you will have to keep this license). However, I am doing everything under Fusion 360 so not sure you will like that...

DEvil0000, 2018-10-04:
> looks like you are using T-Slot mostly and not V-Slot

You are right I am using T-Slot. I was not aware of the difference till now.

> I am doing everything under Fusion 360 so not sure you will like that...

Not much since its quite expensive if you build something occasionally. I know its good and maybe worth it but I build something twice a year up to once a month. OpenScad works fine for me - maybe you can export the models as scad files?

gregsaun, 2018-10-04:
You should have a look to Openbuilds (inventors of the v-slot), they are doing very good job!
https://www.youtube.com/watch?v=584Z47gTBRY
https://openbuilds.com/

I found it much faster to use than Openscad but we all have our own habit. Unfortunately I cannot export a scad file (I even do not know a tool that can do that).

Closed 2019-05-30.

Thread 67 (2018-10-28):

MK3 X-Axis issue

Pathogenius, 2018-10-28:
The last two twist ties on the extruder that hold the cable bundle to that rear arm needed to be removed for XYZ cal to complete, because they cause an end stop, removing them allows for an extra couple of millimeters to the left, thus the extruder then makes the end stop collision properly.

MK3 with R3 extruder

Pathogenius, 2018-10-28:
I neglected to mention probably the main contributing factor, that I am using the X-Axis parts from the 'bear_extruder_and_x_axis', but NOT using the extruder parts themselves.

Pathogenius, 2018-10-28:
I also neglected to mention that the collision is specifically into the RAMBO cover door, which does extend a fair amount in from the frame itself.

gregsaun, 2019-03-12:
Unfortunately the extruder and X axis are made to work together and are not compatible with other projects

Lichtjaeger, 2019-03-12:
It would make me really happy if I can use a bear x-axis with a Prusa extruder someday.

gregsaun, 2019-03-13:
@Lichtjaeger To make this possible I had to redesign how the extruder is assembled in order to have room on the back for the new belt path. I also don't see in what the Prusa extruder could be better than the Bear extruder. What would be the motivation for that?

Lichtjaeger, 2019-03-13:
Sorry, I didn't mean to attack you. You've done an incredible job here.
It's just that, to my knowledge, there is currently no Bear MK3S extruder for MMU2S.

IMO it would be nice to be able to use Prusas latest innovations with your optimized designs. Interchangeable and modular as possible. So we can try both designs and combinations of them without unnecessary effort.

I only have one printer. When I want to try Prusas new extruder I can't replace the extruder only but have to swap the whole x-axis.

gregsaun, 2019-03-13:
Oh sorry for my message, at no moment I thought you were attacking me :-D . I was just asking awkwardly.

I am working on MK3S and should be out this week. MMU2S might take a bit of time but a member of the community is working on a solution right now : https://www.thingiverse.com/thing:3472911

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

Closed 2019-03-12.

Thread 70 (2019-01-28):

Ambiguous extrusion lengths

ax00b3, 2019-01-28:
The BOM says:

> 1x 311mm + 311mm + 290mm,
2x 356mm + 370mm

Is this two of everything and just one 290mm? If so, it should read

> 1x 290mm,
2x 356mm + 370mm + 311mm

Sorry to be a nag, this is the priciest part and I don't want to get it wrong because I overthink stuff.

thespand, 2019-01-28:
Hi ax00b3,
Yes, you are correct :)

Panayiotis-git, 2019-01-28:
I think Greg is trying to optimize the lengths to cut from 1 meter extrusions so you will waste less material.

gregsaun, 2019-05-30:
As this went back few times I know fixed it

Closed 2019-05-30.

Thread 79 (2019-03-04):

MK3S: incompatible belt tensioner

wavexx, 2019-03-04:
Just a heads up:

The MK3S includes a belt tensioner just under the Y carriage, which is pretty nice given that there's no tensioner currently on the full upgrade (I had to play with the Y idler screws).

I thought I could retrofit the MK3S tensioner while doing the full upgrade, but it doesn't work ;)
The MK3 tensioner doesn't have a straight path between the idler and the motor anymore: the path from the idler to the carriage has been moved down due to the screw.

With the bear y idler, the lower path of the belt will touch the MK3 y tensioner when moving towards the LCD and pull the belt up as well. Since the entire tensioner is taller, a 16T idler won't work either.

However, I do still like the MK3S tensioner design :]

gregsaun, 2019-03-12:
Sorry for my late answer, I will create a new Y axis soon that will fix this issue :-)

lsarios9144, 2019-07-25:
Was This issue ever solved? Waiting to order the Bear Frame.

cggorman, 2019-07-25:
Not by Greg but the RHD tensioner is listed by him in the optional parts.  I can confirm it works on my Mk3S.  I'm actually using the toothed (20t, LDO) idler remix, tho.

gregsaun, 2019-07-25:
I am working on it right now ;-)

cggorman, 2019-07-25:
Greg,

Unrelated, but can you explain why the X & Y motor mounts only use three screws?

gregsaun, 2019-08-21:
@cggorman On Y you will hit the belt holder with 4 screws, at least on MK2S/2.5(S). On MK3 it would be too small to be efficient.

gregsaun, 2019-08-21:
This is now fixed with the new release https://github.com/gregsaun/prusa_i3_bear_upgrade/releases/tag/2.1.0-alpha0. Thanks for having reported this!

Closed 2019-08-21.

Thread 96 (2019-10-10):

PSU lower mount

serkanaksu, 2019-10-10:
I‘ve got self adjusting V-Slot Nuts. When I try to fix the PSU lower mount I can‘t fix it because of the missing V-Slot overhang (if it’s called so).

gregsaun, 2019-11-07:
Could you share a link of the t-nut you are using? What lower PSU mount are you using (MK2S, MK2.5(S), MK3(S) grey PSU or MK3(S) black PSU)?

serkanaksu, 2019-11-07:
MK3S silver PSU with the original Prusa Cover.
These are the T-Nuts I'm using.

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

It would be nice, if the mount would have the V-Slot profile.

gregsaun, 2019-11-08:
Are you using this mount?
https://github.com/gregsaun/prusa_i3_bear_upgrade/blob/dev/printed_parts/mk3_mk3s/stl/psu_lower_mount_silver.stl

serkanaksu, 2019-11-08:
Correct!

gregsaun, 2019-11-08:
This PSU mount does not have the vslot alignment tab because some PSU cover are not reliable. For example, some MK2S came with injection molded cover which are not precise at all. Not having the vslot alignment tab makes it easier to adjust for such cases.

Those t-nuts will not work if you have the alignment tab printed because it will collide with the center of the t-nuts.

serkanaksu, 2019-11-08:
I will try to build a custom one :)

gregsaun, 2019-11-08:
Please share what you design, interested to see your idea!

I agree for the PSU cover, for now you can check what there is in the optional parts from the community.

taz43mca, 2019-11-09:
I looked at the 2.1 Alfa and did download the mount. Am waiting for the final of 2.1 before I commit to final assembly. Also. after 3 successful prints last night, after replacing all Y axis rods and bearings, my print tonight had a 1-2 mm shift at about 20mm height (z). I guess that was not the problem. Plenty of grease and no marks on rods. The problem is elsewhere. Any thoughts???
In a message dated 11/8/2019 7:48:15 AM Eastern Standard Time, notifications@github.com writes:

Are you using this mount?
https://github.com/gregsaun/prusa_i3_bear_upgrade/blob/dev/printed_parts/mk3_mk3s/stl/psu_lower_mount_silver.stl

—
You are receiving this because you are subscribed to this thread.
Reply to this email directly, view it on GitHub, or unsubscribe.

Closed 2019-12-17.

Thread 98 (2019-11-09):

Layer shift issue

gregsaun, 2019-11-09:
I looked at the 2.1 Alfa and did download the mount. Am waiting for the final of 2.1 before I commit to final assembly. Also. after 3 successful prints last night, after replacing all Y axis rods and bearings, my print tonight had a 1-2 mm shift at about 20mm height (z). I guess that was not the problem. Plenty of grease and no marks on rods. The problem is elsewhere. Any thoughts???

_Originally posted by @taz43mca in https://github.com/gregsaun/prusa_i3_bear_upgrade/issues/96#issuecomment-552055884_

gregsaun, 2019-11-09:
Hi @taz43mca, I have created a separate issue to better track your problem.

First of all, are you sure the shift is in Y and not X (or both)?

taz43mca, 2019-11-09:
Just in y axis. Also, just did upgrade few to 2.8.1 one other person had similar problem after upgrade. He went back to 2.8.0 and problem went away.On Nov 9, 2019 2:56 AM, Grégoire Saunier <notifications@github.com> wrote:Hi @taz43mca, I have created a separate issue to better track your problem.
First of all, are you sure the shift is in Y and not X (or both)?

—You are receiving this because you were mentioned.Reply to this email directly, view it on GitHub, or unsubscribe.

gregsaun, 2019-11-09:
Do you use bearings from Prusa? Are you using the U bolt or the Bear bearing holders?

taz43mca, 2019-11-10:
The bearings are the original ones from PRUSA. The replacement one are off the shelf as I did not see any ones on the PRUSA web site.I used the original "U" bolts as this is an unmodified (BEAR) printer.After taking the advise of one of the posters and flashed the printer with the older 3.8.0 Firm Ware, the problem went away. Changing the rods and bearings were not a waste but seems something is wrong with FW 3.8.1.Note the BEAR bearing holders will not clear the PRUSA original frame. Tried that. Have now had the printer running for a 15H 30 M print and now a 7 Hour print and NO PROBLEM or SHIFT. Used both PLA and PETG and Sliced with the latest Slicer update.Hope this helps.Note, I am building a MK3  BEAR from the ground up. Like the BEAR Frame, Updated Extruder and x axis belt tensioner, and other improvements.

In a message dated 11/9/2019 1:20:54 PM Eastern Standard Time, notifications@github.com writes:

Do you use bearings from Prusa? Are you using the U bolt or the Bear bearing holders?

—
You are receiving this because you were mentioned.
Reply to this email directly, view it on GitHub, or unsubscribe.

gregsaun, 2019-11-11:
Thank you for those information. On the Prusa's github there is an issue talking layer shift after a power panic occured. Did you had a power outage recently?

In the meantime it could be great to double check the distance of your smooth rods. Use a caliper and measure directly from rod to rod directly. If your caliper is too short, you can sometimes remove the little end stop at the end of your caliper and have a bit more length (generally enough to measure the inner distance).

taz43mca, 2019-11-12:
No power loss/outage or panicThought of it and did measure space between rods, all checks out. Did that when I replaced rods and bearings, also checked belt tension, greased the bearingsflashed 3.8.0 firmware (had done recent flash of 3.8.1 before problems started)then I printed 3 objects: 15+ hours, 6+ hours and 3+ hours with no shift and all prints as good as with new printer.Two of these were printed from the same files that had been a problem before. One was a new slice.Note: I have 3D printed a spacer that makes sure rods are spaced exactly as required.
Has anyone checked FW update 3.8.1 on a MK25 to see if it gives  print shifts. They may have to print a tall and large object to check. As of right now I will continue using FW update 3.8.0 as it works.
In a message dated 11/11/2019 12:26:36 PM Eastern Standard Time, notifications@github.com writes:

Thank you for those information. On the Prusa's github there is an issue talking layer shift after a power panic occured. Did you had a power outage recently?

In the meantime it could be great to double check the distance of your smooth rods. Use a caliper and measure directly from rod to rod directly. If your caliper is too short, you can sometimes remove the little end stop at the end of your caliper and have a bit more length (generally enough to measure the inner distance).

—
You are receiving this because you were mentioned.
Reply to this email directly, view it on GitHub, or unsubscribe.

gregsaun, 2019-11-12:
I could not find someone reporting that on the Prusa's github, maybe it could be great to report one then.

Indulae, 2019-11-16:
I have the same issue of layer shifting only on y axis.

taz43mca, 2019-11-16:
are you using a Prusa i3 2.5 or 3 and FirmWare update 3.8.1?I went back to FW update 3.8.0 and problem went away.
In a message dated 11/16/2019 3:24:52 AM Eastern Standard Time, notifications@github.com writes:

I have the same issue of layer shifting only on y axis.

—
You are receiving this because you were mentioned.
Reply to this email directly, view it on GitHub, or unsubscribe.

taz43mca, 2019-12-01:
In discussing this issue on the PRUSAPRINTER.com blof/forum, one person noted that he has reflashed his printer with the 3.8.0 firmware and that solved the problem. I had done the same thing and the problem went away. I have just done two prints, one at 197mm that at the 194mm level has what appears to be incomplete OUTside layer. The infill appears to be there but the outside smooth layer does not. The other print as 134mm high and had a similar problem at the 126mm layer. I can take pictures of both (note that this is when I am using the 3.8.0 firmware. I have updated my slicer and drivers to the latest posted on the PRUSA web site. I have a WIN 10 pro OS.
Your thoughts?Merrill Albury
In a message dated 11/11/2019 12:26:36 PM Eastern Standard Time, notifications@github.com writes:

Thank you for those information. On the Prusa's github there is an issue talking layer shift after a power panic occured. Did you had a power outage recently?

In the meantime it could be great to double check the distance of your smooth rods. Use a caliper and measure directly from rod to rod directly. If your caliper is too short, you can sometimes remove the little end stop at the end of your caliper and have a bit more length (generally enough to measure the inner distance).

—
You are receiving this because you were mentioned.
Reply to this email directly, view it on GitHub, or unsubscribe.

gregsaun, 2019-12-05:
Sorry for my late answer. Could you share a picture of your printer? Sorry to ask for that but most of the time a picture/video saves tons of word.

In the meantime, check that your X axis and your filament aren't catch by sometimes when you reach top of Z axis.

Closed 2020-03-10.

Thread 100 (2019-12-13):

Y Motor Mount Lower Extrusion screw too short

ctilley83, 2019-12-13:
The new revised Y motor (2.1) mount no longer utilizes the same length screw for the bottom screw hole.  For those with version 2.0 frames, this conversion requires a screw that is 4mm longer than the v2.0 version.  This could be remedied by deepening the pocket for the lower horizontally facing extrusion mounting hole so the existing screw will properly engage the t nut. Would make it easier for people upgrading parts to utilize the same hardware.

gregsaun, 2019-12-13:
I tried to do that but it isn't possible. The minimum acceptable would be M5x15mm screw to not hit the M3 screw. However, 15mm screws is not a standard length (even if sold by Openbuilds) and to give us the choice to use better screws and user to source easily the parts we went to M5x16mm screw.

If you make it shorter you will have a hole in the M3 screw path which can affect the tightening of the stepper (lots of vibrations at this location).

You can see all this in the drawing bellow. The 11mm length in bottom is the M5x16mm length (5mm goes inside the t-nut). The 5mm on the left is half of the space needed for the M5 screw head.
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

ctilley83, 2019-12-13:
Gotcha. I see now.

Closed 2019-12-14.

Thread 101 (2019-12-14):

New 2.1 assembly manual

taz43mca, 2019-12-14:
Any idea when the new 2.1 assembly guide will be finished. I have downloaded the temporary guide but am waiting for the finished product since I see discussions about it are still in progress.
I had made spacers for the 2.0 version (MK 3) to ensure that all parts are properly placed and have also done similar spacers for the 2.1 (so far mods). As a note, I had made similar spacers for the old MK2/2.5 but since the kits are all MK3 did not want to post and confuse the issues. Have similar reservations about those made for the 2.0 since the 2.1 parts are different and require some spacers to be modified.
Thanks for all who are working to make a better printer. Hard to do since we daily see new and "better" ways to do things.

gregsaun, 2019-12-16:
I am working on the RC1 now and in parallel to the new hardware with my manufacturer. Once RC1 will be published I will start working on the assembly guide.

RC1 will include new build helpers for Y and Z axis. I push them to the dev branch last week:
https://github.com/gregsaun/prusa_i3_bear_upgrade/blob/dev/printed_parts/common_to_all_versions/stl/build_helper_y.stl
https://github.com/gregsaun/prusa_i3_bear_upgrade/blob/dev/printed_parts/common_to_all_versions/stl/build_helper_z.stl

The Y axis helper is going to be used like this:
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
Be careful to use it only on the left side and not both sides! It is not made to set the width of the smooth rods.

Do you have some images about those spacers, I am interested to see what you made?

taz43mca, 2019-12-17:
I have numerous photos. I will see if I can zip them small enough to send. Although I have been designing and producing spacers for all the variations, I will just zip those for the latest (MK3 frame and 2.1) changes.
I have not posted them to thingiverse nor have any experience with that site but planned to do so in the near future. Any suggestions?Carl
In a message dated 12/16/2019 4:07:40 AM Eastern Standard Time, notifications@github.com writes:

I am working on the RC1 now and in parallel to the new hardware with my manufacturer. Once RC1 will be published I will start working on the assembly guide.

RC1 will include new build helpers for Y and Z axis. I push them to the dev branch last week:
https://github.com/gregsaun/prusa_i3_bear_upgrade/blob/dev/printed_parts/common_to_all_versions/stl/build_helper_y.stl
https://github.com/gregsaun/prusa_i3_bear_upgrade/blob/dev/printed_parts/common_to_all_versions/stl/build_helper_z.stl

The Y axis helper is going to be used like this:

Be careful to use it only on the left side and not both sides! It is not made to set the width of the smooth rods.

Do you have some images about those spacers, I am interested to see what you made?

—
You are receiving this because you authored the thread.
Reply to this email directly, view it on GitHub, or unsubscribe.

gregsaun, 2019-12-17:
The problem with printed spacers/helpers is that they can be inaccurate. Some people have badly calibrated printer and dimensions or accuracy can be wrong. This is why, for example, I recommend a quality square to build the frame and do not provide printed part.

taz43mca, 2019-12-17:
Mine measured just fine but understand your argument. Thanks for the feedback.On Dec 17, 2019 3:36 AM, Grégoire Saunier <notifications@github.com> wrote:The problem with printed spacers/helpers is that they can be inaccurate. Some people have badly calibrated printer and dimensions or accuracy can be wrong. This is why, for example, I recommend a quality square to build the frame and do not provide printed part.

—You are receiving this because you authored the thread.Reply to this email directly, view it on GitHub, or unsubscribe.

stelgenhof, 2020-01-18:
@gregsaun Looking forward to the new manual. I'm currently working on the v2.1 upgrade for my MK2.5 and a single overall manual would be very welcome :) Not a major burden, but now I have to navigate between the two branches to see if I follow everything in the right order.

gregsaun, 2020-01-19:
@stelgenhof The new manual is going to be like the Bear extruder. Keep in mind that 2.1 is still under development so for now the manual is just here to help assembly but will removed later.

taz43mca, 2020-01-19:
I am building a Prusa Mk3/Bear hybrid from scratch. Jut finished the Bear X axis extruder upgrade. I agree, a new 2.1 manual would sure make things easier. I have also noted that some of the items, like the Z axis motor mount shown in some drawings are different from the original Bear upgrade so I designed and printed them on my own. Makes the task of getting the motors level and at the right height much easier. I have done some more tweeking with other parts and designing and printing some spacers that make assembly much easier. As they say, the proof is in the pudding. Will post when I finish.
In a message dated 1/18/2020 6:48:04 AM Eastern Standard Time, notifications@github.com writes:

@gregsaun Looking forward to the new manual. I'm currently working on the v2.1 upgrade for my MK2.5 and a single overall manual would be very welcome :) Not a major burden, but now I have to navigate between the two branches to see if I follow everything in the right order.

—
You are receiving this because you authored the thread.
Reply to this email directly, view it on GitHub, or unsubscribe.

taz43mca, 2020-02-18:
Could not find a way to ask this but:
Build a Prusa MK3S Bear. Downloaded latest firmware (FW) 3.8.1 and flashed Rambo board. (did twice). Started self test. completed all motor and temp tests, when it got to the XYZ test/cal it tested movement of X and Y axis and the Z axis. All worked ok until nozzle moved to bed to do the 4 point leveling check. As soon as nozzle reached the bed, it stopped and I got a calibration error. Unit did NOT do any circular search as my MK2.5 does. It just reached the bed and stopped (not touching). I did a complete check of all my measurements and as per error procedures and Bear assembly manual, and all are OK. Did a reflash of the FW. Same results.
The Rambo board was acquired from ALL3D (dropped shipped). I could maybe understand if the printer ran a circular search before it gave the error but did not. I DID NOT press the reset button on Rambo board but thought I might do that and then reflash again. HELP!
Suggestions???

taz43mca, 2020-02-26:
I built a Prusa MK3S with the 2.1 mod., including the Bear extruder upgrade and I have a problem. All tests are OK until it starts the 1-4 bed Z axis cal. When the extruder comes down to the bed it stops and says calibration failure. I have reset and reflashed the Einsy board with various versions of the MK3S software and no luch. The PINDA tests fine and all XYZ axis checks say correct. If I do an auto home cal it does the cal over the target. When I do the XYZ cal that starts with and auto home it appears to do the test OK, raises the Z axis to the top, tells me to clean the nozzle, put a sheet of paper on the, no metal sheet. When I press the nob to start the test the extruder comes down and stops withing a mm of the bed, with the PINDA about 5mm to the left of the edge of the target circle
20200225_175327
and says calibration failed...refer to manual.
I have rechecked all my measurements and all are correct. What I did notice is that when the extruder goes all the way to the left and stops at the Z axis frame, the nozzle is about 3-4mm short of the 250mm line on the bed. When the nozzle is moved all the way to the right, it is 3-4mm past the edge of the bed.
Thought of moving the bed 3-5 mm to the right so that the nozzle is in line with the left dotted 250mm line when up against the stops but then the PINDA would be even further to the left of the target. The bed rails would no longer be 82mm from either side as shown in the drawings.
I have been fighting this for days and working with Jason at Ultimachine trying to resolve.
Any suggestions???

taz43mca, 2020-02-26:
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
   Here is a photo of where the PINDA sets

taz43mca, 2020-02-27:
With more extensive checking, the offset is 2.3 to 3 mm to the left

stelgenhof, 2020-08-24:
Awesome! @gregsaun Thanks for all the hard work. My v2.1 was just completed this weekend, with a first successful test print :)

gregsaun, 2020-08-25:
@stelgenhof Happy to read that, enjoy!

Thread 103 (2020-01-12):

Y tensioner idler - small range

ochm, 2020-01-12:
2.1 tensioner idler have small range for movement. I made small modification, range for open is now full.
[y_idler_tensioner-trimed-corner.zip](https://github.com/gregsaun/prusa_i3_bear_upgrade/files/4050683/y_idler_tensioner-trimed-corner.zip)
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

gregsaun, 2020-01-12:
This was made on purpose mainly for those two reasons :
  - Due to the pivot point you change the position of the belt (on the Z axis) while tensioning. It is currently designed to have a change of 0.03mm which is lower than belt tolerance and printed part tolerance. However, if y a user is opening too much the tensioner it could create too much difference in the position of the belt.
  - too much opening will make the idler less stiff and might become fragile

Closed 2020-03-10.

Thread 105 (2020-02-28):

Mk3 calibration failure with Bear 2.1 build.

taz43mca, 2020-02-28:
Unfortunately I posted my last on this on the 2.1 manual discussion. But here goes again.
Built a Prusa Mk3S from scratch using the Bear upgrade with the 2.1 mod. Also the bear extruder mod.
The kit came from a listed source including the Einsy Rambo which was dropped shipped with the Prusa software installed. Other PRUSA parts as needed.  Assembly went OK and all measurements checked OK.
Per Prusa instructions I downloaded the latest FW and SW from PRUSA web site (FW 3.8.1).
Started the full calibration and tests. XYZ motors, bed and extruder heater went OK. Got to the Z axis 4 point cal and after it went all the way to the top, had me clean the brand new nozzle and put a sheet of paper on the bed, tell them that there was no steel plate on the bed, it moved down to the bed and IMMEDIATELY said calibration failure. I have downloaded and reloaded the firmware (after doing the hard reset), even older versions 3.6.1; rechecked all my measurements; did a complete PINDA check and still get the same results. I tried an Autohome test and it did that right over the target but when it does one before the Z cal, it is over the side of the bed (the PINDA is about 2mm to the left and 2mm to the front of the target.
Then I noticed that when the extruder was all the way to the left it was 2mm to the right of the left print edge line (extruder is against the stops) and when it fully to the right, it is about 2mm outside the right edge of the board. The Y axis rods are exactly 82mm from the ends of the V slot per instuctions. I have been discussing this with Ultimachine (Jason) and he has given me many things to check but the results are the same. It is interesting to note that when I do the PRUSA hard reset per their instructions, it says it is fully reset but as soon as the printer starts up I get a "choose a language" and then it goes right to the PRUSA calibration menu. Seems that the hard reset does not fully clear the EEPROM of all PRUSA information. Maybe that is as it should be but if I bypass the test and it goes to the regular print screen it looks like the FW is still on the EEPROM. I thought about doing a couple of things:
1. press the reset button that is actually on the Einsy Rambo board - cannot find exactly what that does.
2. move the bed rails 2mm to the right so that, looking from the front, the left is 84mm from the end and the right is 80mm from the end. I would also have to move the Y axis motor and the idler 2mm to the right. This would, however, move the PINDA ferther to the right of the target when the extruder in the fuly right position but would put the nozzle directly over the left print line.
I have attached a PDF drawing of what I have right now.
HELP!
[Bear Drawing problem.pdf](https://github.com/gregsaun/prusa_i3_bear_upgrade/files/4269488/Bear.Drawing.problem.pdf)

gregsaun, 2020-03-10:
I have just realize I missed that issue, sorry for my late answer!

With the Bear extruder you have to use the Bear Calibration firmware as explained in the manual here:
https://guides.bear-lab.com/Guide/5.+Final+adjustments+and+calibration/14?lang=en#s244

This should fix your issue.

taz43mca, 2020-03-11:
In talking to Jason Reynolds at Ultimachine, he asked me to try the MK3 FW vice the MK3S. The MK3 did a cal with no problem except it would not recognize the "S" upgraded filament sensor. I thne reflashed with the <K3S FW and it failed as before. I assume that I need to do a factory reset of the printer and then reflash with the Bear FW, then reflash with the MK3S FW (no reset). BUT it would appear that I would need to use the BEAR FW if I found a need to recalibrate the printer for any reason. True?Regards,Merrill
In a message dated 3/10/2020 1:05:17 PM Eastern Standard Time, notifications@github.com writes:

I have just realize I missed that issue, sorry for my late answer!

With the Bear extruder you have to use the Bear Calibration firmware as explained in the manual here:
https://guides.bear-lab.com/Guide/5.+Final+adjustments+and+calibration/14?lang=en#s244

This should fix your issue.

—
You are receiving this because you authored the thread.
Reply to this email directly, view it on GitHub, or unsubscribe.

gregsaun, 2020-03-11:
Yes you need to use the Bear calibration firmware as explained in our assembly guide. Prusa has changed the geometry of the extruder between MK3 and MK3S. Z height is a little different and so calibration fails with Bear extruder which uses a similar geometry than MK3. The Bear extruder didn't follow the MK3S design because we found that it can create several potential print quality issues as well as lowering the reliability.

taz43mca, 2020-03-11:
If I read this correctly, are you saying that I am better using the Bear FW for the future as it corrects the Prusa FW problems? If that is true then future Prusa MK3S FW upgrades would have to be complimented by a like Bear FW update. And does the difference in the FW still give you the extra 10mm (210 vs 200) not had with the MK2/2.5? Not that this is a game breaker.Regards,MerrillPS: I will give you feedback on how the calibration and subsequent print goes with the Bear FW.

In a message dated 3/11/2020 3:21:05 AM Eastern Standard Time, notifications@github.com writes:

Yes you need to use the Bear calibration firmware as explained in our assembly guide. Prusa has changed the geometry of the extruder between MK3 and MK3S. Z height is a little different and so calibration fails with Bear extruder which uses a similar geometry than MK3. The Bear extruder didn't follow the MK3S design because we found that it can create several potential print quality issues as well as lowering the reliability.

—
You are receiving this because you authored the thread.
Reply to this email directly, view it on GitHub, or unsubscribe.

taz43mca, 2020-03-12:
Update:I have not put it through all its paces yet but did a small test print that is acceptable. More Z cal may be needed to tune it.So what happened: I followed the instructions exactly but since I did a new build and not a modified MK3, the printer did not recognize the filament sensor and the Z axis test failed. So I went back and used the Wizard that tests everything and that did the trick. So a new build has to do things differently then a modified build.I plan to do some of my more intricate builds with color changes and see how it is doing...using the BEAR FW. Then I MAY load the Prusa FW and see how that does. When I loaded the file to print the printer told me to update the FW to 3.8.1 but I just clicked through it and when ahead and did the print.Why, you may ask, well I had some interesting problems with 3.8.1 FW and my MK2.5 (not 2.5S) and noticed that some others also had the same problem with layer shift. So my MK2.5 is running the 3.8.0 FW with no problem.After I put the Bear MK3S clone through its paces and after I use it with the Prusa 3.8.1 FW, I will give you a final update.For now, thanks,Merrill
In a message dated 3/11/2020 3:21:05 AM Eastern Standard Time, notifications@github.com writes:

Yes you need to use the Bear calibration firmware as explained in our assembly guide. Prusa has changed the geometry of the extruder between MK3 and MK3S. Z height is a little different and so calibration fails with Bear extruder which uses a similar geometry than MK3. The Bear extruder didn't follow the MK3S design because we found that it can create several potential print quality issues as well as lowering the reliability.

—
You are receiving this because you authored the thread.
Reply to this email directly, view it on GitHub, or unsubscribe.

taz43mca, 2020-03-13:
A follow up to my printing and using the Bear FW.I have a problem and don't know why. Using the Bear FW and the Prusa latest FW for the MK3S I have the same problem. When it starts to print after doing the 9 point check, it goes to the side and says "unload filament" I do that and then "load filament" and it returns to the bed and immediately does it again. It keeps repeating this. I tried using the Prusa slicer on two different computer to slice the print and write the g code; I used both an SD card and Pointerface with a USB cable to print the item, and still got the same results. So I disabled the filament sensor and got it to print. Any ideas why this is happening??? I thought all my troubles were over with flashing and doing a claibration with the Bear FW. This is new. Interesting that I was able to do a print without this problem after the initial wizard calibration. Nothing changed except I turned off the printer and turned it back on. I only made changes AFTER the problem appeared.Regards,Merrill
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
taz43mca, 2020-03-20:
After the 4 h 53 m print, I disconnected the filament sensor and tried to print with the menu in the normal position (not in Support...Sensor State selection) and it failed as before. I think that eliminates the filament sensor as the problem.Since it prints OK when the menu selection is "Support...Sensor State" , it still leaves the firmware (which has been flashed lastly to PRUSA MK3S ver 3.8.1. Same results as when I tried to print in the BEAR FW so think that may eliminate the firmware. That leaves the Ensiy Rambo and the LCD panel. Both of which I find hard to believe is the cause of the problem but seems there is no other choices.Thoughts.Regards,Merrill
In a message dated 3/16/2020 3:02:15 PM Eastern Standard Time, carlalbury@hotmail.com writes:

The video is well over the limit for sending. But here is what I tried:

Sliced as         SD Card to print                    Menu at Support; Sensor State      When pressing knob

MK3S              Failed after 9 point check    Printed OK                 until                Failed

MK3                Failed after 9 point check    Printed OL                  until                Failed  (note when loading file the printer said this was not correct printer..do I want to continue)

MK3S              Failed after 9 point check    Printed OK                 until it stopped to change color then failed after filament change (had to press knob to make the change so got

 out of “support: sensor state” menu selection.

(Note: I set this up for a color manual change at .40mm as set up in Prusa slicer)

Could this be an LCD panel or (heaven forbid) an Enisy Rambo problem? Or maybe something in the software although I have had the same problem with the Bear FW and Prusa FW.

Sent from  Mail for Windows 10

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

taz43mca, 2020-03-23:
Just got a post on the forum that said they had same problem with the printer going to "filament remove" position. They did a complete reset of printer and problem cleared. If I do that then I guess I will lose all calibration data and will have to flash with the Bear FW, recalibrate printer, then reflash with Prusa FW. Or is there a way around it.

taz43mca, 2020-03-28:
Tried but no help.

taz43mca, 2020-03-30:
Success. The IR lever was not tripping the IR sensor, even when it and IR sensor were physically removed from the extruder body and manually moved together. I reprinted the sensor lever using a .05mm layer setting and it works fine. I should have noted that the "0" reading for the IR sensor was wrong but didn't.
Thanks for all the help. My Bear Prusa MK3S Clone with a Bear frame and extruder appears to be working fine. Hope I do not have the need to bring problems with this clone back to the forum.
Two good points: I learned a lot more about my printer than I knew before; and, it now works as designed.
The extruder was much easier to work on with the BEAR build than the Prusa instructions to fix a similar problem on their new extruder body.
I assume that when I do my 2.5 to 2.5S upgrade (next) that I will be able to know all the different things I need to do to use the BEAR extruder.
I have printed a few extra .05mm layered levers so I will not have the same problem.

Closed 2020-03-31.

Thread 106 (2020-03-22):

Rod length issue with ver 2.1 and mk2 optional build parts

johnpaularthur, 2020-03-22:
I was noticing that the y-axis vslot is 311mm but with the optional build parts y axis rod holders, it would require the rods to be about the same length since the rod slots do not extend past the x-axis vslot.  But since the mk2 rods are 320mm, they would not fit.   Or am I missing something?

gregsaun, 2020-03-31:
Looks like there is an issue with parts listed for 2.1 on Full Bear 2.0 MK2/2.5 frame, the y_rod_holder is the wrong part. Please use this one in the meantime:
https://github.com/gregsaun/prusa_i3_bear_upgrade/blob/master/full_upgrade/for_mk2.5/printed_parts/stl/rod_holder.stl

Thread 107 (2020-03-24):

MK3S print failure in most Menu modes

taz43mca, 2020-03-24:
I have a MK3S with the Bear Frame  and Bear Extruder upgrades. Having worked through a few problems the printer does a great job BUT only if I put the menu on the LCD in the "Support...Sensor State" mode. If not in that mode, the printer does the 9 point bed check, goes to the start point and immediately goes to the right corner and gives me a "Filament remove" message, after doing that and replacing the filament, it returns to the left corner start point and repeats the same.
I have checked all connections and even disconnected the filament sensor but same results, Also reflashed with latest FW, disabled the filament sensor, with same results.
The Autoload and unload work as designed otherwise.
One person posted that they did a complete printer reset and the problem went away, not sure if they were talking about my particular problem, but I have not done that yet as I am not sure if I will then have to load the Bear FW and do an XYZ calibration, a complete wizard printer check, or whatever???
I also saw that some people had reported that some connections on their LCD to Enisy board had to be changed due to a problem.
I tried using Prontoface and the USB to print but got same results if the LCD is in any menu setting other than "Support...Sensor State".
Tried slicing on two different computers, using MK2.5, 2.5S, 3, 3S with same results except that the printer did recognize that I had not sliced in the 3S setting. I tried to print anyway and same results in all.
Finally, If I am printing in the "Support...Sensor State" menu mode and press the knob on the LCD, then the print stops and starts the crazy "filament removal process" repeatedly as before. I even tried to go back to the "Support...Sensor State" menu selection after the filament reload but that did not work to stop the cycle.

taz43mca, 2020-03-28:
Tried to completely reset the printer and use the BEAR FW to recalibrate all over again from scratch. Same results. Then flashed the Prusa 3.8.1 FW same results. I guess the person who did this and was successful was just lucky or maybe he did something I am not aware of. Printer is still humming along in the "Support...Sensor State" menu setting but no where else.

gregsaun, 2020-03-31:
Did you solved this issue? I am asking because other issue you wrote 😉

taz43mca, 2020-04-01:
All of my issues with the BEAR MK3 PRUSA clone I just finished a two color print with no problems (not using a MMU) using the Prusa slicer to set up color changes.All the help from many sources got me to this point. Hope my mistakes and problems help others when doing such a build. That includes GitHub, PRUSA, Ultimachine (both people and forums and procedures.Regards,Merrill AlburyStay healthy.
In a message dated 3/31/2020 7:55:18 AM Eastern Standard Time, notifications@github.com writes:

Did you solved this issue? I am asking because other issue you wrote 😉

—
You are receiving this because you authored the thread.
Reply to this email directly, view it on GitHub, or unsubscribe.

Closed 2020-04-01.

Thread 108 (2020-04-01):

Calibration failed! Check the axes and run again

Idus, 2020-04-01:
So, I finally got the time to do my full Bear upgrade from a MK3s. I have been using the Bear x-ends and the Bear x-carriage for my MK3s Bondtech BMG extruder for over a year already (https://www.thingiverse.com/thing:3477926). Alos, made sure to get the new 2.1 RC-1 parts.

I´ve now spent a couple of hours trying to fine-tune where the PINDA2 aims on the heatbed to get through the XYZ Calibration... but always getting "**Calibration failed! Check the axes and run again**".

However, I have realized something... If I run "Self Test" - all works out just fine. And as stated in step 20 in the latest RC-1 bear manual - the PINDA2 **IS** within the circle on the heatbed when it lowers during "Self Test". It is the exact same spot where the nozzle goes over the heatbed when I pick "Auto Home". (see pic.)

But if I run the "XYZ Calibration" (or Z "Calibration") - it moves to start in _another spot_ and stops before even continuing and failing... again.

Pinda2 have been calibrated to be "a cable-strap higher" than the nozzle as well as -0,5, +1, +1,5 and +2mm - all same results.

Note: Currently running latest Prusa FW 3.8.1 (and have tried with 3.9.0 beta))

**So, really stuck and don´t know what more to do?** 😕 Cannot find any solution in the manual or any forums. I´ve asked this in the Facebook-group as well - but no useful feedback.

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

gregsaun, 2020-04-01:
Hi Idus, you need to use the Bontech firmware:
https://support.bondtech.se/Guide/00.+Bondtech+Prusa+i3+-+Firmware+Update/44

Hope that helps!

taz43mca, 2020-04-01:
I had all the same problems. Used the suggested FW but unlike the directions, I did a complete system reset, flashed the Bear FW and then used the Wizard to do a complete calibration. After all done, then flashed with Prusa 3.8.1 FW for Mk 3S. Had one more unrelated problem but this fixed the "failed" problem. There is a long history of all this in the forum.On Apr 1, 2020 12:54 PM, Grégoire Saunier <notifications@github.com> wrote:
Hi Idus, you need to use the Bontech firmware:
https://support.bondtech.se/Guide/00.+Bondtech+Prusa+i3+-+Firmware+Update/44
Hope that helps!

—You are receiving this because you are subscribed to this thread.Reply to this email directly, view it on GitHub, or unsubscribe.

Idus, 2020-04-01:
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

SUCCESS!! :-D You are the guru!

I have used original Prusa FW with the additional Bondtech M-commands for stepping (and the Bear x-ends/carriage) for over a year without any additional need for change anything else to calibrate etc, so never thought that the firmware needed to change when doing the full Bear.

All calibrated and working just fine - both smooth and textured plates.

Merci beaucoup and greetings from Sweden!

Closed 2020-04-01.

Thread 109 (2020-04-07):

v2.1 Z Motor Mount - Shaft coupler clearance

trevjonez, 2020-04-07:
with the latest parts I am finding the clearance is just barely an issue.

older design looks to have a slimmer deck on the z axis (unconfirmed) compared to the 2.1 additionally the hole above the motor is smaller once past the nema 17 indexing step.

Issue is that on the newer design if you are using motors with a coupler clamp to drive your lead screws the hot end fan will bottom out on the coupler.

I have modified the parts for my own needs and that is literally what is printing in the image of the printer with 2.1 parts. So this is non blocking for me, but I thought you should know.

I opted to open the hole to make it work as the nema 17 alignment in the tapered opening and rod bottoming out on the motor relative to the 2040 seem to be the critical element. Certainly I have removed material so maybe deflection becomes an issue, but I believe it will be non critical.

here is my modified part: https://a360.co/2Xf1bkr
sketch 12, extrude 25, chamfer 19, and fillet 7 in that save are new edits from me. although the numbering is likely off due to me removing a few elements before making my changes. (uncofirmed, maybe numbering doesn't get affected by me deleting other features?)

old version of parts:
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

newer version:
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

My specific coupler need only slide ~2mm lower to provide the coupler and fan enough clearance.

gregsaun, 2020-04-29:
Nice modification, I prefer to not add this on my parts as this is not a good idea to use coupler there. Also, the smaller center helps for stiffness so I prefer to keep it like that for now. However, could you share this somewhere and I add it to the optional parts from the community?

Gwyki, 2020-05-09:
@trevjonez do you not suffer with z-wobble nonsense with a coupler there? Your white parts do seem to show periodic z artefacts...

I came looking as I have had one of my screw integrated motors fail and was going to replace them with a coupler but ran into the clearance issue on my bear upgrade that you described. If it is a pain to tweak to get concentric, etc then I will just buy a new stepper! :/

trevjonez, 2020-05-10:
@Gwyki
I have been fighting with z-wobble the whole time. biggest issue is just getting decent lead-screws.

I finally broke down and ordered some custom motors from LDO for my machines this last week.

You are spot on about the lines on my X ends. The interval on them is 2mm which coincides with the lead of the screw and is exactly the type of thing z wobble causes. Though with adjustment on the machine I was able to minimize it on future parts. but it comes back just about any time I adjust things and I have to repeat the effort of minimizing it.

@gregsaun
Given the likely low usage of such a part I don't think I will upload the stl's to any distro site. I feel that anyone wishing to follow this path will either modify the parts on their own or find my F360 link in [the original post](https://github.com/gregsaun/prusa_i3_bear_upgrade/issues/109#issue-595599410)

And I totally agree it isn't ideal to have the coupler, but I wanted the higher resolution leadscrew to minimize backlash without resorting to spring based nuts. Custom motors will finally get me to the best of both worlds.

Closed 2020-05-10.

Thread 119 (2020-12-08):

Custom Z-height: Changed Z_MAX_POS accordingly but Z-Calibration fails

Demolux, 2020-12-08:
Hi there,

I recently bought 2 bear upgrades and decided to increase the z height to about 569 mm.

I am using the firmware 3.9.2 release and compiled it via Ubuntu.

I changed `Z_MAX_POS` to `569 `but i guess that is not enough:

1. The printer always goes to the top end leveling the Z axis.
2. Then it asks for nozzle cleaning.
3. After confirmation the Z axis goes down
4. It tops about 10mm above the bed aborting the calibration "Z calibration failed, check axis".

-> Changing `Z_MAX_POS` to `555` or `565` did not change that behaviour.

I looked around the web to find an explanation what is needed to change in the FW in order to run a successful Z-calibration with modified Z but was not successful.

May you explain what is needed to be changed besides `Z_MAX_POS`?
The only other modification I made was uncomment `#define FILAMENTCHANGE_ZADD 2` because otherwise I got compilation errors (Z exceeding 256).

Thank you very much.

Demolux, 2020-12-17:
Turns out 5 mm below the max. travel distance in Z was the sweet spot where at least calibrate Z worked!

Closed 2020-12-17.

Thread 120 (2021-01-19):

optional LCD cover does not fit the lcd supports (version 2.1)

domhardt, 2021-01-19:
The optional [LCD cover with text](https://github.com/gregsaun/prusa_i3_bear_upgrade/blob/master/optional_parts/lcd_cover/printed_parts/stl/lcd_cover_text.stl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) has not enough space in the back to fit the [lcd_support_a](https://github.com/gregsaun/prusa_i3_bear_upgrade/blob/master/optional_parts/lcd_cover/printed_parts/stl/lcd_support_a.stl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) and [lcd_support_b](https://github.com/gregsaun/prusa_i3_bear_upgrade/blob/master/optional_parts/lcd_cover/printed_parts/stl/lcd_support_b.stl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). I refer to the version 2.1

gregsaun, 2021-01-20:
Hello, are you using the official Prusa LCD screen or an LDO Motor one?

domhardt, 2021-01-22:
Hello, as I got my printer from someone else I had to re-check everything. All dimensions of my parts are identical to the components from the Fusion360 project of this repo. So in the next step I assembled the components in Fusion360 and there is not enough space in the LCD cover for the LCD support brackets. Please see the attached images and the [Fusio360 project](https://a360.co/2LOxcg5).

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

gregsaun, 2021-01-23:
Oh I see, you are not using the correct mount. The custom cover comes with different mounts that are attached with 4 M3x10 screws. Check lcd_support_a and lcd_support_b here: https://github.com/gregsaun/prusa_i3_bear_upgrade/tree/master/optional_parts/lcd_cover/printed_parts/stl . (note the lcd_support_x_prusa is for original Prusa frame)

domhardt, 2021-01-23:
> Oh I see, you are not using the correct mount. The custom cover comes with different mounts that are attached with 4 M3x10 screws. Check lcd_support_a and lcd_support_b here: https://github.com/gregsaun/prusa_i3_bear_upgrade/tree/master/optional_parts/lcd_cover/printed_parts/stl . (note the lcd_support_x_prusa is for original Prusa frame)

Oh, sorry. This is my fault then. Thank you for clarifying that. I will close this issue then. Sorry for bothering you.

Keep on the good work!

Closed 2021-01-23.

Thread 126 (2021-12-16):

MK3 Y carriage with endstop switch

Neukam, 2021-12-16:
I'm converting a MK1 style clone into what will essentially be a MK2.5S Bear using Prusa Firmware for Ramps.  I ordered a MK52 bed and MK3 Y carriage.  I will not have sensorless homing, so I will need to use endstop switches.  Will the MK2 motor/idler/belt/bearing mounts work with the MK3 Y carriage?

floridaservices, 2022-01-01:
My mk25s bear has end stops.  I have a rambo board but that should not make a difference.  I think you will just need to use the mk25 y motor mount, and if you are using the prusa mk3s+ parts for your x-axis just drill some holes in the left carriage piece to mount the x stop.  I have a mk52 12v and 24v bed,the mounting differences and bed support will not keep you from using endstops.  My mk25s started life as a mk1 with a wood frame and a mk2b heatbed

Neukam, 2022-01-01:
I've done some comparison on the DXF of both Y carriages and modified the MK3 belt holder to trigger the endstop.  I will be using the MK2 bearing holders.  I think I have a solution that will work correctly, but I haven't assembled and tested it yet.

floridaservices, 2022-01-01:
That is the difference I understand.  I have a 12V MK52 bed with the old style mounting so I was able to use the bear 2.5S y belt holder.  I don't do much design modification but it might be easier to modify the belt holder to fit the MK3 bed support, then you can use it with the 2.5S Y-motor holder.  I never figured out Prusa's reasoning for swapping the Y motor around but if you want to stick with the MK3 firmware you would have to do what you are planning but also modify the y-axis motor mount.

Neukam, 2022-01-01:
The plan is to use all MK2 mounts with a modified MK3 Y belt holder.  The modified belt holder has an extension added to trigger the endstop attached to the MK2 Y motor mount.  Assuming i calculated the offset correctly, and assuming the 24v bed aligns to the carriage in the same position as the 12v bed, the modified belt holder should work.

floridaservices, 2022-01-01:
I think it will work for you, it has been a while since I have had either of my printers apart that far but I seem to recall that the general location of the belt mount on both variations of the bed is the same, but they changed the screw spacing just enough.  I would work in some adjustment room if you can so you don't have to tweak firmware, unless you enjoy that sort of thing :)

floridaservices, 2022-01-15:
Came across this tonight, maybe this will help you: https://www.thingiverse.com/thing:3468567

Neukam, 2022-01-15:
I appreciate the input.  I have made a modified belt mount that should work with the MK3/MK52 carriage on a MK2 bear.  When i get a chance to finish the wiring and test it, I will report back and I'll post the modified part to thingiverse and link it here.

GMagician, 2022-02-14:
[y_belt_holder.zip](https://github.com/gregsaun/prusa_i3_bear_upgrade/files/8064184/y_belt_holder.zip)

These are what I used on my bear 2.1. I didn't use sensorless home not so reliable to me. And I readded switch. Please note that belt holder is mirrored compared to original bear 2.1 and motor support has to be mounted in a different position

Neukam, 2022-02-15:
I should have updated and closed this issue a while ago, but I had a hard drive die and lost the STL that I made.  I still have the GCode I used in Octoprint, so I'm currently reprinting the part.  I will measure the part that I am printing and recreate an STL so that I can upload it.  I feel guilty that I have held this issue open so long and I plan to close this issue tonight.  Thanks to all who have replied.

Neukam, 2022-02-15:
[y_belt_holder_MK3_Endstop.zip](https://github.com/gregsaun/prusa_i3_bear_upgrade/files/8065513/y_belt_holder_MK3_Endstop.zip)

I have uploaded the modified y_belt_holder above and also at prusaprinters.org.  [Here is the link](https://www.prusaprinters.org/prints/134527-prusa-bear-21-mk52-y-belt-holder-with-endstop).

Closed 2022-02-15.

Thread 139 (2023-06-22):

Nexquito | Nextruder Mosquito hotend

ByJuix, 2023-06-22:
Hey there, I plan to modify the Nextruder to allow a Slice Engineering Mosquito hotend to be mounted. I'm sure it'll be a bit of a challenge :D

**TLDR:**
I would appreciate it if somebody with a MK4 could try to attach some weight to the extruder and see if the first layer calibration succeeds.

---------
I own a Prusa MK3S+ Bear and would like to keep my Mosquito hotend. I ordered the MK4 upgrade kit, but I think it won't ship within the next two weeks; therefore, it would be good to know if the first layer calibration still succeeds if there is added weight on the extruder assembly. The Mosquito is roughly 10g to 15g heavier than the stock Nextruder heatblock; also there are other printed parts needed, in total it will be around 20g to 30g heavier.

To make this work, the Mosquito will be mounted on top of the loadcell and the gearbox and motor have to be inverted to stick out the front so that the filament can be fed into the heatbreak, that whole construction then has to be turned so that the nozzle can be aligned with the regular position.

Is it worth the hassle? Probably not, but it would be cool to know if it's possible and maybe @BondtechAB can design a better solution.

_Originally posted by @ByJuix in https://github.com/gregsaun/prusa_i3_bear_upgrade/issues/138#issuecomment-1601633566_

ByJuix, 2023-06-22:
I created a quick sketch to visualize my idea.

The red part represents the loadcell, the gray part the fan. I'm not certain how to mount the mosquito, but I think I will get some ideas within the next couple of days. [The nozzles are at the exact same location]
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

Closed 2025-06-24.

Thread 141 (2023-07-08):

MK4 carriage on MK3S bearing holder

clicktoselect, 2023-07-08:
I had to get a new carriage for my MK3s and Prusa only sell the mk4 one now. The bearing holders aren’t quite big/deep enough to actually make contact with the carriage once the screws are tightened so they are sort of floating there. Has anyone else had this issue or found a solution? I know it’s a bit of a weird issue having mk4 carriage on mk3

gregsaun, 2023-07-08:
Hi @clicktoselect , thanks for reporting this, I was actually wondering how Prusa ship things regarding this. Did you receive the metal bearing clips with the carriage? Those in green in this page:
https://help.prusa3d.com/guide/2a-y-axis-assembly_406654#407495

clicktoselect, 2023-07-08:
It came by itself only, no bearing clips included sadly

gregsaun, 2023-07-08:
Looks like there is an issue with Prusa, they should have send you the bearing clips. Bearing clips have been introduced with MK3S+ which means if you are on MK3S you don't have those (it was U bolt at that time) and so the carriage they sell isn't compatible with MK3S. Might be good to talk to the support.

MK3S kit bed bearings assembly (steps 24 to 27): https://help.prusa3d.com/guide/2-y-axis-assembly_25488#26528
MK3(S) to MK3S+ upgrade (steps 4 to 7): https://help.prusa3d.com/guide/5-y-axis-upgrade_194395#194732

On MK4 they have added bearing pads and plastic pads, I would ask the support if you could get those too. See the step 12 here:
https://help.prusa3d.com/guide/7-y-carriage-heatbed-assembly_438310#438578

I am not able to update those parts at the moment but I will update the assembly guide to explain that the new carriage should be used with the bearing clips.

Please let me know how it goes with the support :)

clicktoselect, 2023-07-08:
Thanks for your help Greg. I'll get in contact with Prusa support and see if they can offer me any of the new clips and pads. Thanks again!

gregsaun, 2023-07-08:
Good luck 👍

clicktoselect, 2023-09-25:
Just to follow up on this. I noticed the other day that the MK3s+ assembly manual now shows the new carriage, and does not actually require those pads that the mk4 has (https://help.prusa3d.com/guide/2a-y-axis-assembly_406654#408670)

In this case, it should be fine to just use the prusa bearing clips for the bear frame, instead of using the specific bear y bearing clips?

gregsaun, 2023-12-18:
I think the Bear version makes the Yvaxis a bit more silent. But both are fine.

sl1pkn07, 2025-05-10:
hi

i think prusa mixed up the instructions from MK4/S in the MK3/S, because few steps forward, still show the old Y carriage
https://help.prusa3d.com/guide/7-heatbed-psu-assembly_172872#173408

i think this because the new carriage needs the new hotbed spacers (https://www.prusa3d.com/es/producto/expansion-joints-set/) instead of the old ones (the hex spacers)

greetings

gregsaun, 2025-06-24:
As there is no more activity here I close this issue. Feel free to reopen in case of.

Closed 2025-06-24.

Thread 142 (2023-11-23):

Tune/change filament from LCD-menu causes misalignment

FrHePo, 2023-11-23:
**Printer data:**
Printer type: MK3S
Printer firmware version: 3.13.2
Print via SD card
Bear parts: Lecktor Technologies OÜ - Värvi 5 C400-1 - 10621 Tallinn - Estonia
The Y-axis extrusion length is 331mm
All parts are original Bear.
The distance between the Y-rodholders is 311mm. The distance between the left side bearings is 93.8mm. This results in a max. build-plate travel of 217.2mm. The position of the Z-profiles was determined with the printed build_helper_z.stl-part (106 +/- 0.5mm). Mine measured 105.6mm.
See also: https://github.com/prusa3d/Prusa-Firmware/issues/4498

**Problem description:**
When changing filament during printing with the LCD-function <Tune/change filament> the print head doesn't return to the correct position creating a Y-misalignment of about +0.7mm.
After I noticed this I did a cube test print (see picture) which confirmed me that this misalignment is independent of the printed object or the G-code. It's obvious that when the build-plate travels to the change filament position it runs into the Y-limit (by 0.7mm) which is actually an unintended collision.

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

FrHePo, 2023-11-24:
@gregsaun My (outside/max.) distance between the left side bearings is 93.8mm. Could you check this please?
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

gregsaun, 2023-11-24:
Sorry I can't check CAD for noeàw but you can open the source file to check (Fusion 360).

I am wondering if the distance of the nozzle or the Pinda is closer to the X axis than what it should be. Where is this extruder coning from?

FrHePo, 2023-11-24:
The extruder is not involved in this problem. It's the build-plate that can't travel far enough (by only 0.7mm!) to reach the hard coded (firmware) filament change position. When calling the filament change by LCD-menu the build-plate is moved to the filament change position. My build-plate can't reach this position by 0.7mm. The left-side Y-bearing bangs into the Y-rodholder and can't travel any further.
My extruder is a combination of the Orbiter 2.0 and the E3D Revo Micro.

FrHePo, 2023-11-24:
3d-gussner stated: _We have defined [FILAMENTCHANGE_[XPOS|YPOS|ZADD] = X211 Y0 Z+2](https://github.com/prusa3d/Prusa-Firmware/blob/v3.13.2/Firmware/variants/MK3S.h#L359-L361) which are fine for our printers. And normally the Y axis can travel from [Y-4 up to 212.5] so for the stock printers it has some tolerances._
Standard MK3S Y-travel is [Y-4 up to 212.5]: 216.5mm
My max. Bear Y-travel is 217.2mm. So the max. Y-travel is not the problem. This leaves only 2 options for me: 1. The Y-bearings position is incorrect or 2. The position of the Z-profiles (frame) is incorrect and must be moved 5mm backwards.
The 1st option seems impossible to me. The Y-bearing-position cannot be incorrect by 5mm. That leaves only option 2 which means that the position of the Z-profiles (frame) is incorrect.

FrHePo, 2023-11-24:
Standard MK3:
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

My Extruder:
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

gregsaun, 2023-11-24:
You can check the dimensions of the frame here:
https://github.com/gregsaun/prusa_i3_bear_upgrade/blob/master/mechanical_drawings/bear21_frame_size.pdf

But Yes I suspect it is your extruder. Probably during calibration they stock somewhere the 0.0 point and would be different for you.

FrHePo, 2023-11-24:
Ok. I'll correct the Pinda position and hope and see :-))

FrHePo, 2023-11-26:
@gregsaun / @3d-gussner
After correcting the Y-Pinda-position by 3.5mm the misalignment has been cured. Thanks for your support! It made me a little wiser :-))
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

gregsaun, 2023-11-26:
Good news. I close it then.

Closed 2023-11-26.

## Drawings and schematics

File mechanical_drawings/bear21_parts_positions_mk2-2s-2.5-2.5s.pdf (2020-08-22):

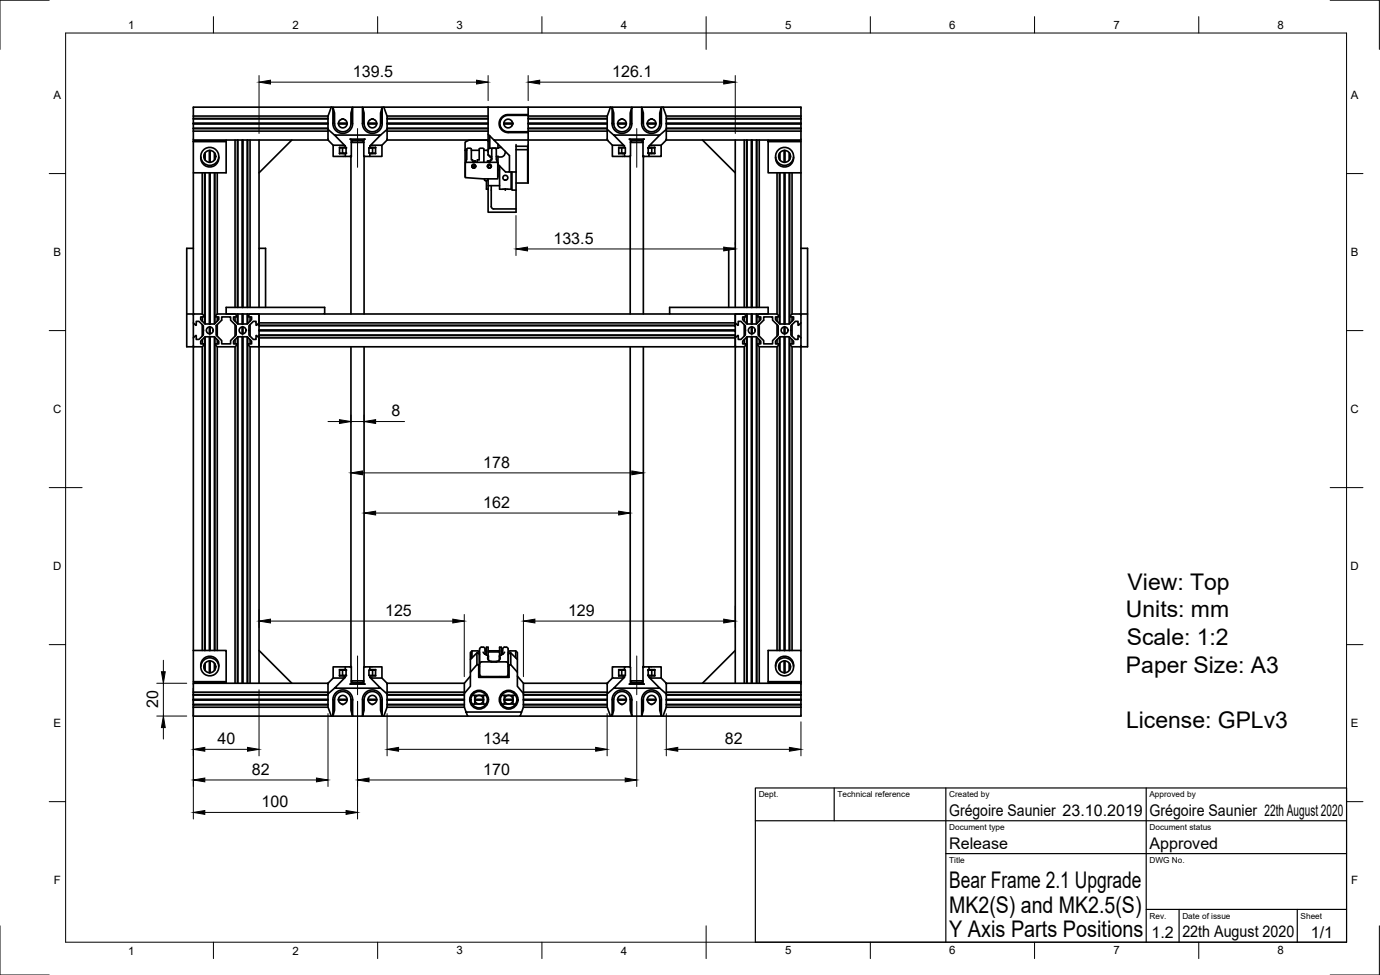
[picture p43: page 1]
View: Top Units: mm Scale: 1:2 Paper Size: A3; License: GPLv3

Dept. | Technical reference | Created by Grégoire Saunier 23.10.2019 | Approved by Grégoire Saunier 22th August 2020

Document type Release | Document status Approved

Title Bear Frame 2.1 Upgrade MK2(S) and MK2.5(S) Y Axis Parts Positions | DWG No.

Rev. 1.2 | Date of issue 22th August 2020 | Sheet 1/1

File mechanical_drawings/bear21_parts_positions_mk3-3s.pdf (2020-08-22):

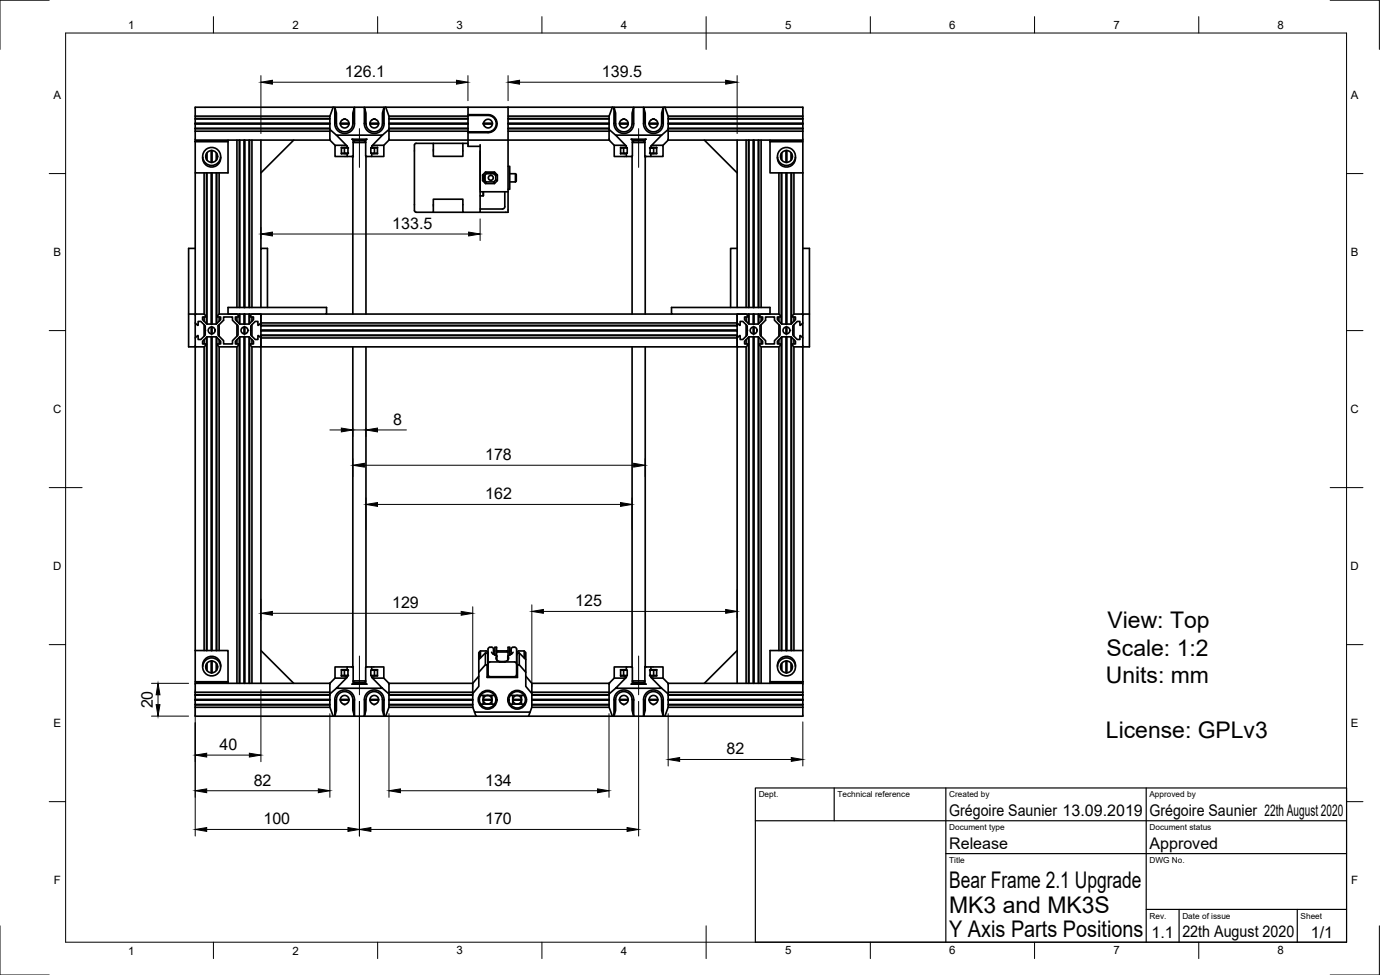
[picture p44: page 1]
View: Top Scale: 1:2 Units: mm; License: GPLv3

Dept. | Technical reference | Created by Grégoire Saunier 13.09.2019 | Approved by Grégoire Saunier 170 22th August 2020

Document type Release | Document status Approved

Title Bear Frame 2.1 Upgrade MK3 and MK3S Y Axis Parts Positions | DWG No.

Rev. 1.1 | Date of issue 22th August 2020 | Sheet 1/1

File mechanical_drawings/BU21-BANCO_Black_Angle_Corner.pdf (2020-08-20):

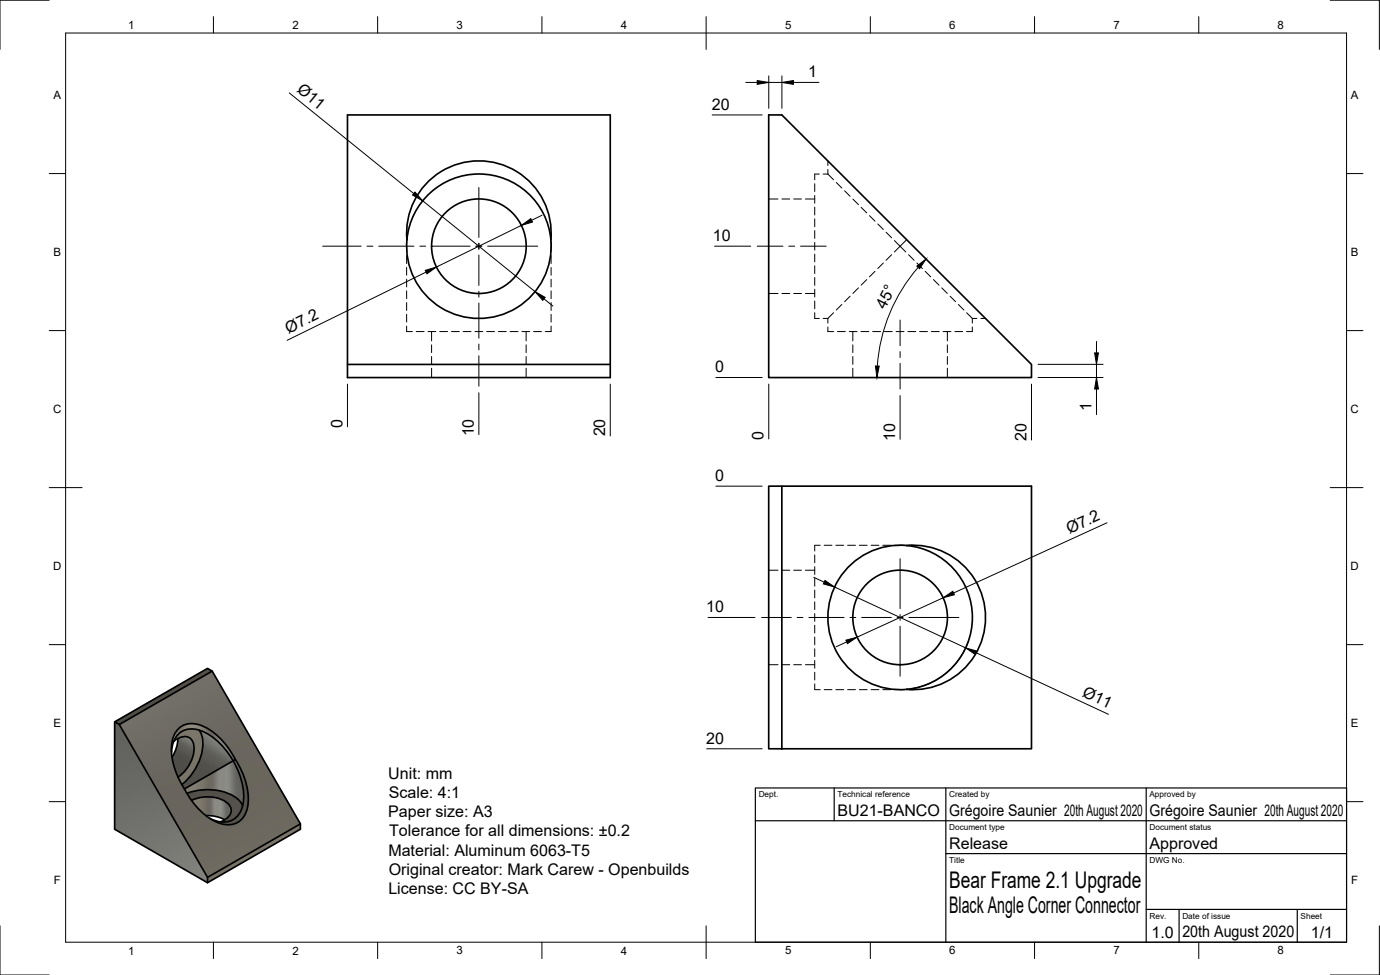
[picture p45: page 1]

Unit: mm
Scale: 4:1
Paper size: A3
Tolerance for all dimensions: ±0.2
Material: Aluminum 6063-T5
Original creator: Mark Carew - Openbuilds
License: CC BY-SA

Dept. | Technical reference BU21-BANCO | Created by Grégoire Saunier 20th August 2020 | Approved by Grégoire Saunier 20th August 2020

Document type Release | Document status Approved

Title Bear Frame 2.1 Upgrade Black Angle Corner Connector | DWG No.

Rev. 1.0 | Date of issue 20th August 2020 | Sheet 1/1

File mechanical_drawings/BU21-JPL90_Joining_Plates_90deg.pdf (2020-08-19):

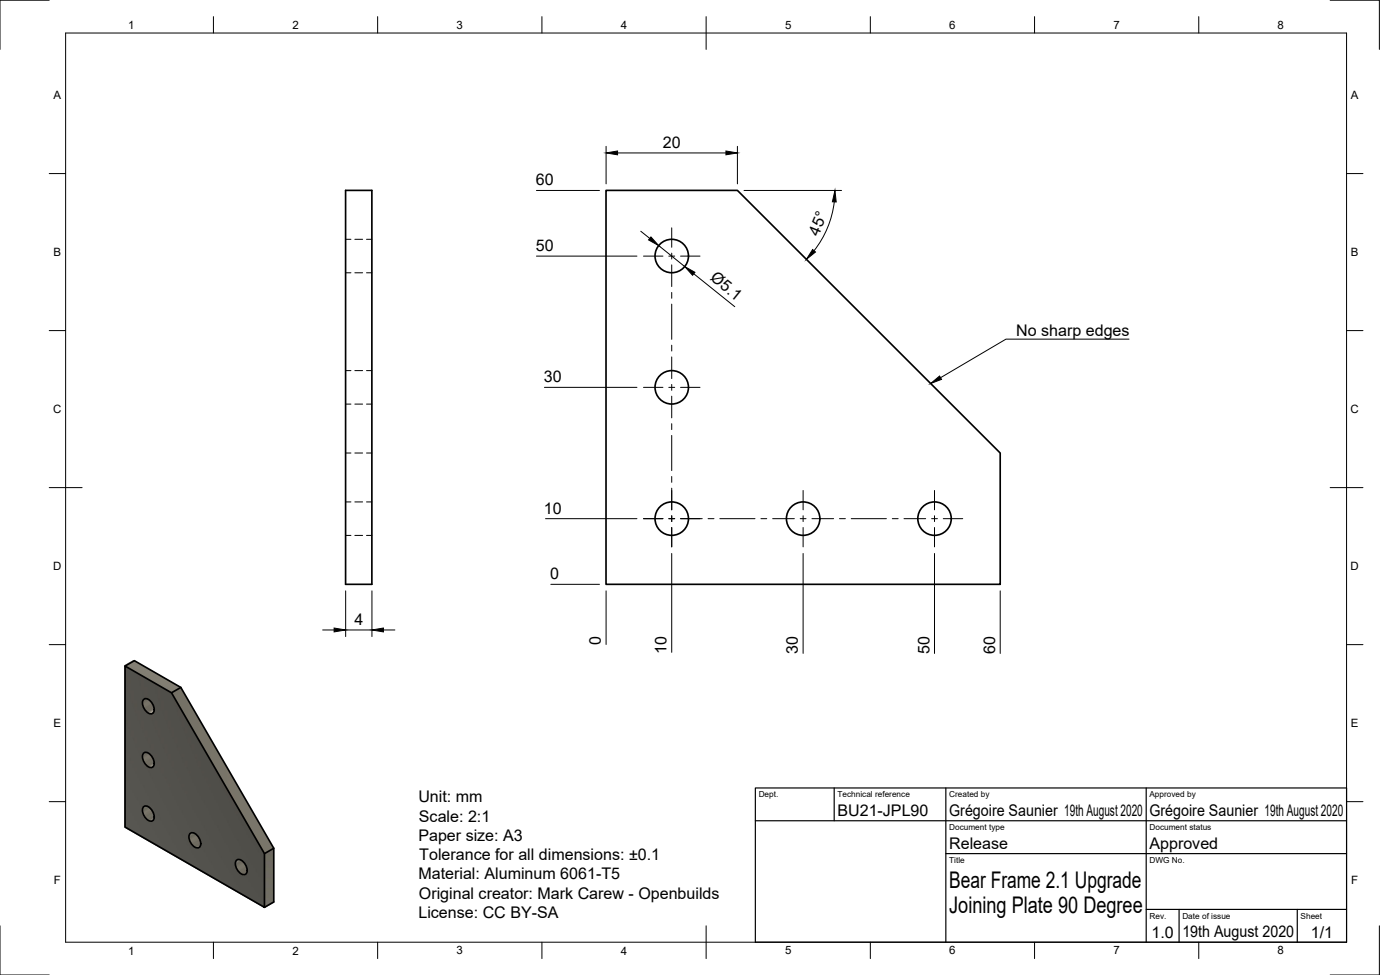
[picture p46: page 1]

No sharp edges

Unit: mm
Scale: 2:1
Paper size: A3
Tolerance for all dimensions: ±0.1
Material: Aluminum 6061-T5
Original creator: Mark Carew - Openbuilds
License: CC BY-SA

Dept. | Technical reference BU21-JPL90 | Created by Grégoire Saunier 19th August 2020 | Approved by Grégoire Saunier 19th August 2020

Document type Release | Document status Approved

Title Bear Frame 2.1 Upgrade Joining Plate 90 Degree | DWG No.

Rev. 1.0 | Date of issue 19th August 2020 | Sheet 1/1

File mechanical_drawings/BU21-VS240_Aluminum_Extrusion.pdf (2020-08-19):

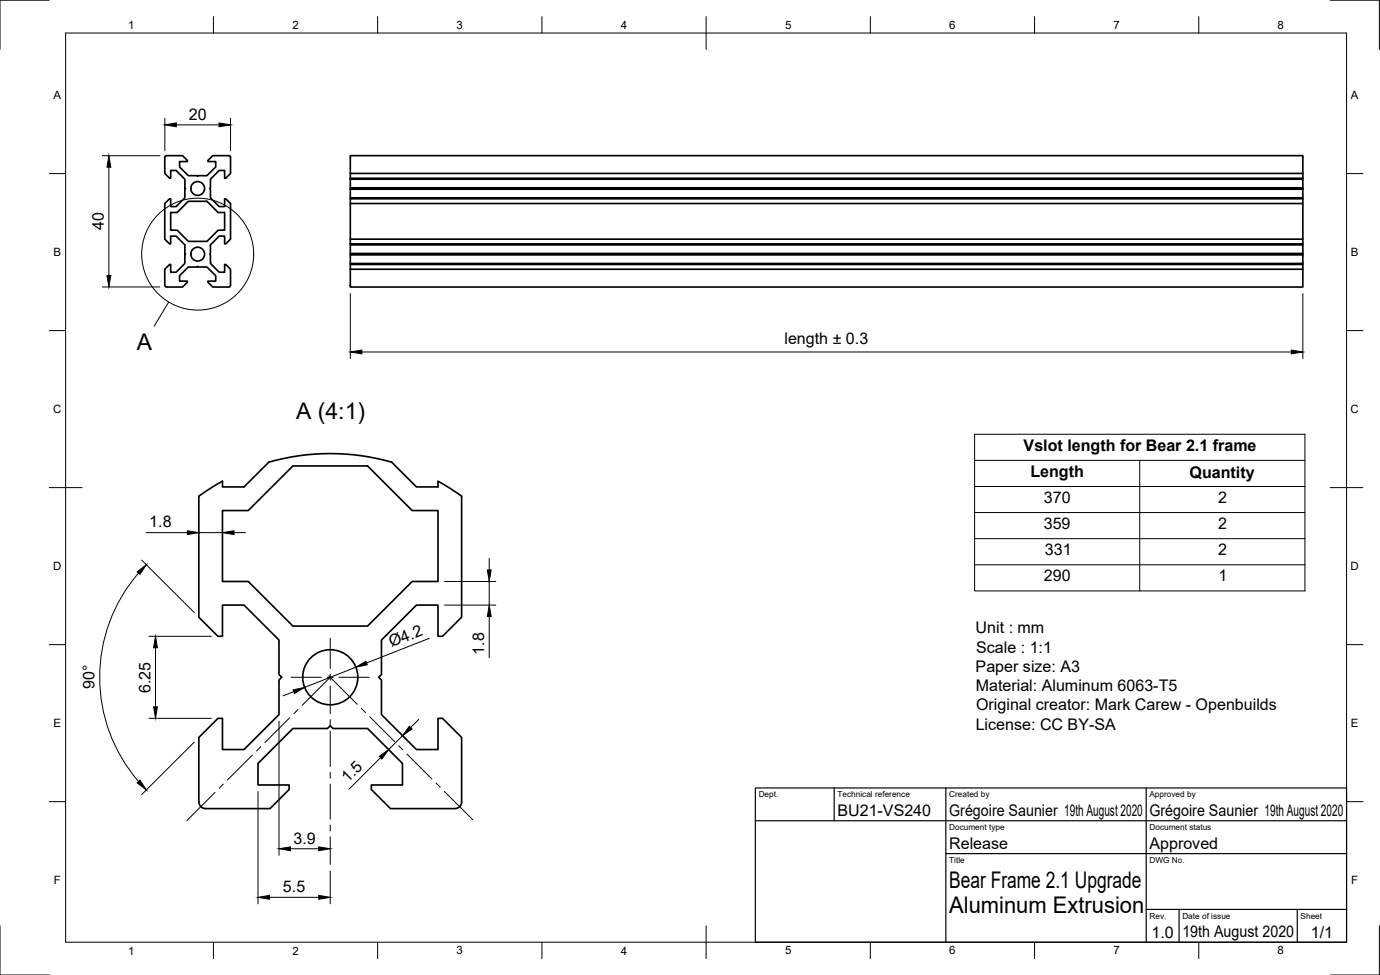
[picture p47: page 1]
length ± 0.3 40

Vslot length for Bear 2.1 frame

Length | Quantity
370 | 2
359 | 2
331 | 2
290 | 1

Unit : mm
Scale : 1:1
Paper size: A3
Material: Aluminum 6063-T5
Original creator: Mark Carew - Openbuilds
License: CC BY-SA

Dept. | Technical reference BU21-VS240 | Created by Grégoire Saunier 19th August 2020 | Approved by Grégoire Saunier 19th August 2020

Document type Release | Document status Approved

Title Bear Frame 2.1 Upgrade Aluminum Extrusion | DWG No.

Rev. 1.0 | Date of issue 19th August 2020 | Sheet 1/1

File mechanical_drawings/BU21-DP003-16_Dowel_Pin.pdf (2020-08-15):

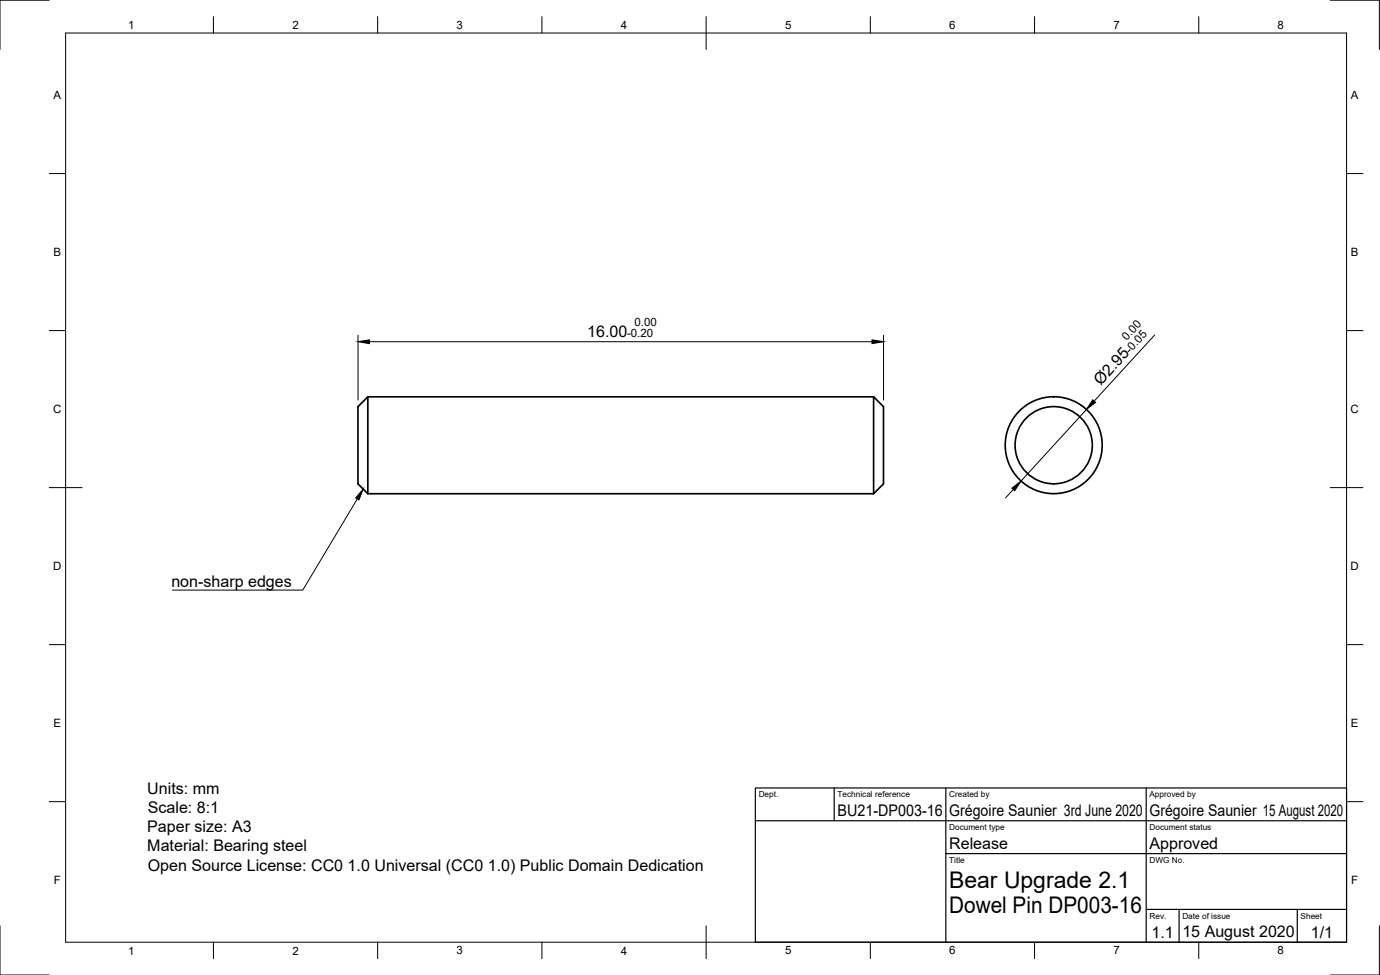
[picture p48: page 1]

non-sharp edges

Units: mm
Scale: 8:1
Paper size: A3
Material: Bearing steel
Open Source License: CC0 1.0 Universal (CC0 1.0) Public Domain Dedication

Dept. | Technical reference BU21-DP003-16 | Created by Grégoire Saunier 3rd June 2020 | Approved by Grégoire Saunier 15 August 2020

Document type Release | Document status Approved

Title Bear Upgrade 2.1 Dowel Pin DP003-16 | DWG No.

Rev. 1.1 | Date of issue 15 August 2020 | Sheet 1/1

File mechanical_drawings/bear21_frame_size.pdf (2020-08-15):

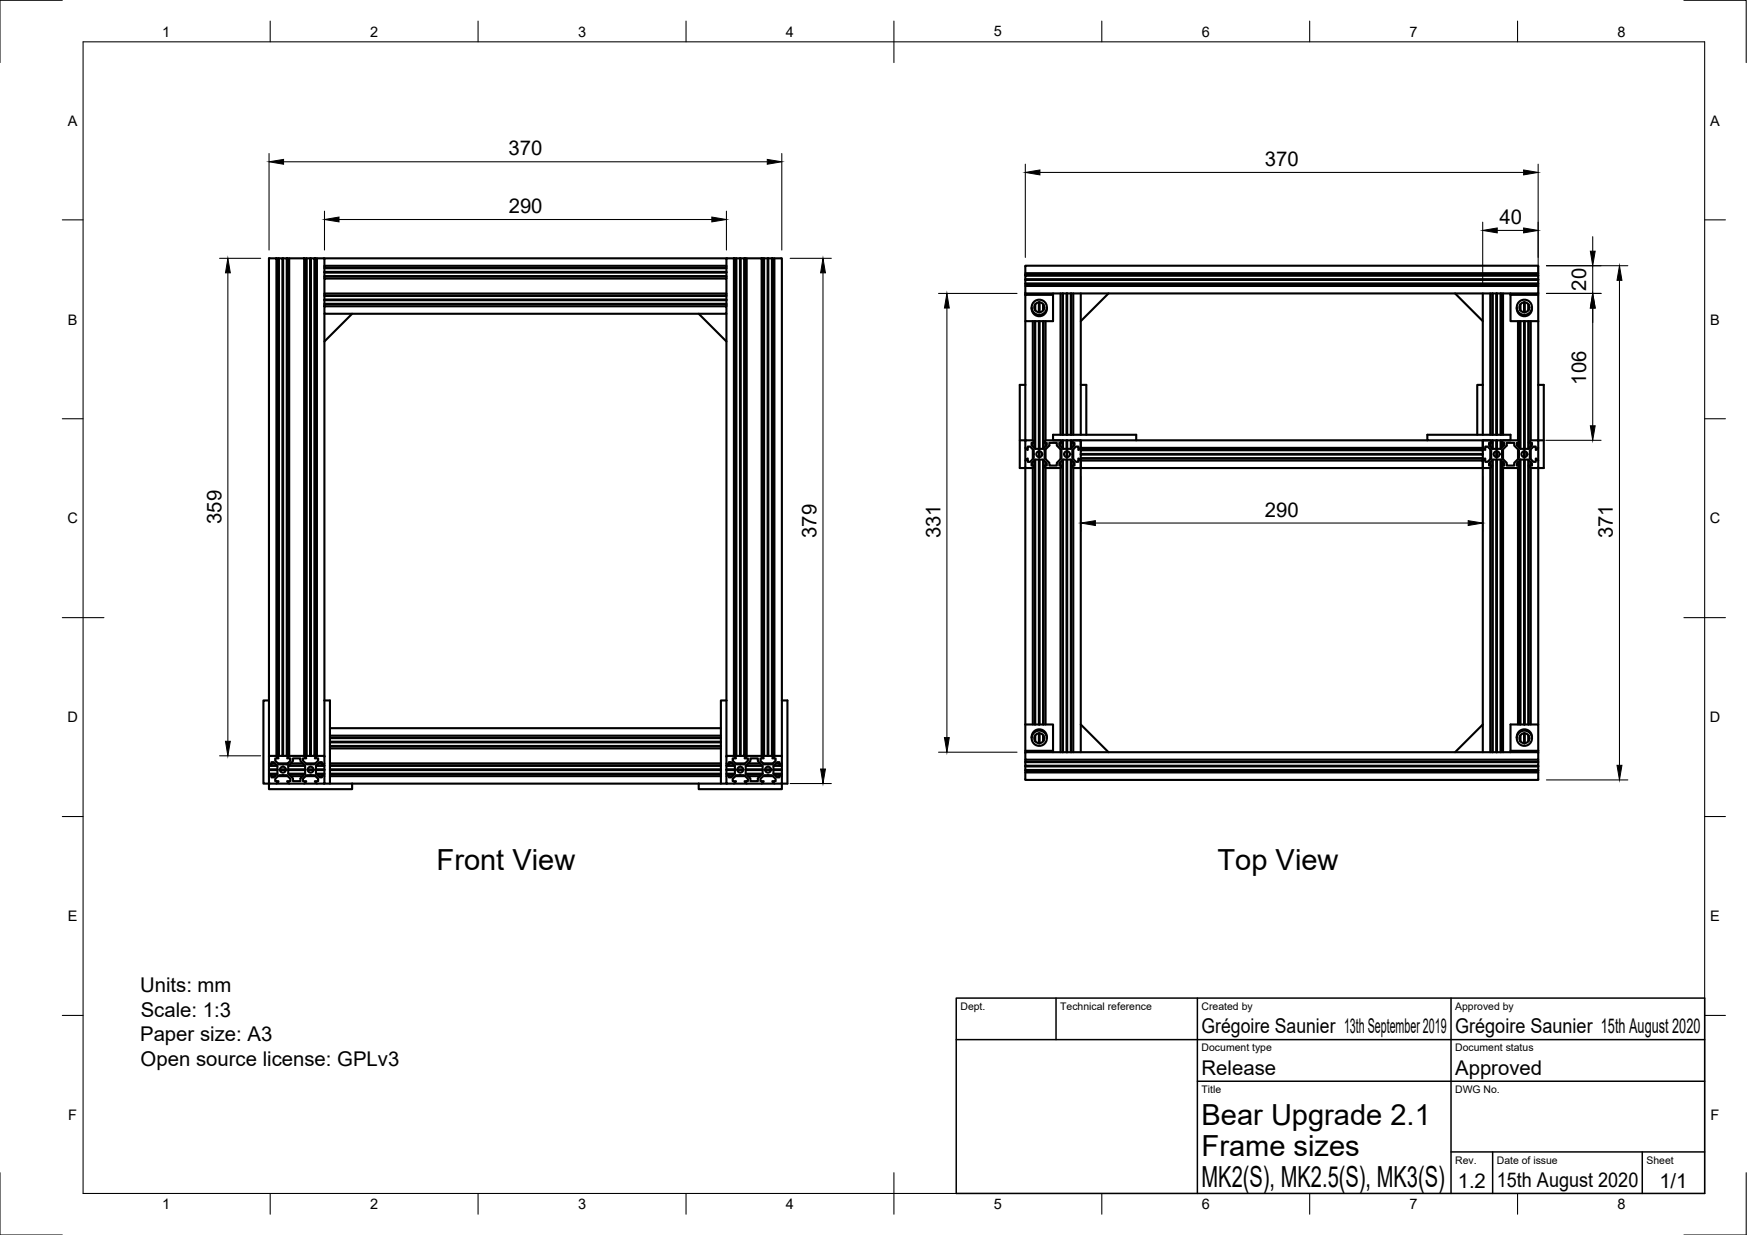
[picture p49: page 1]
Front View; Top View; Units: mm Scale: 1:3 Paper size: A3; Open source license: GPLv3

Dept. | Technical reference | Created by Grégoire Saunier 13th September 2019 | Approved by Grégoire Saunier 15th August 2020

Document type Release | Document status Approved

Title Bear Upgrade 2.1 Frame sizes MK2(S), MK2.5(S), MK3(S) | DWG No.

Rev. 1.2 | Date of issue 15th August 2020 | Sheet 1/1

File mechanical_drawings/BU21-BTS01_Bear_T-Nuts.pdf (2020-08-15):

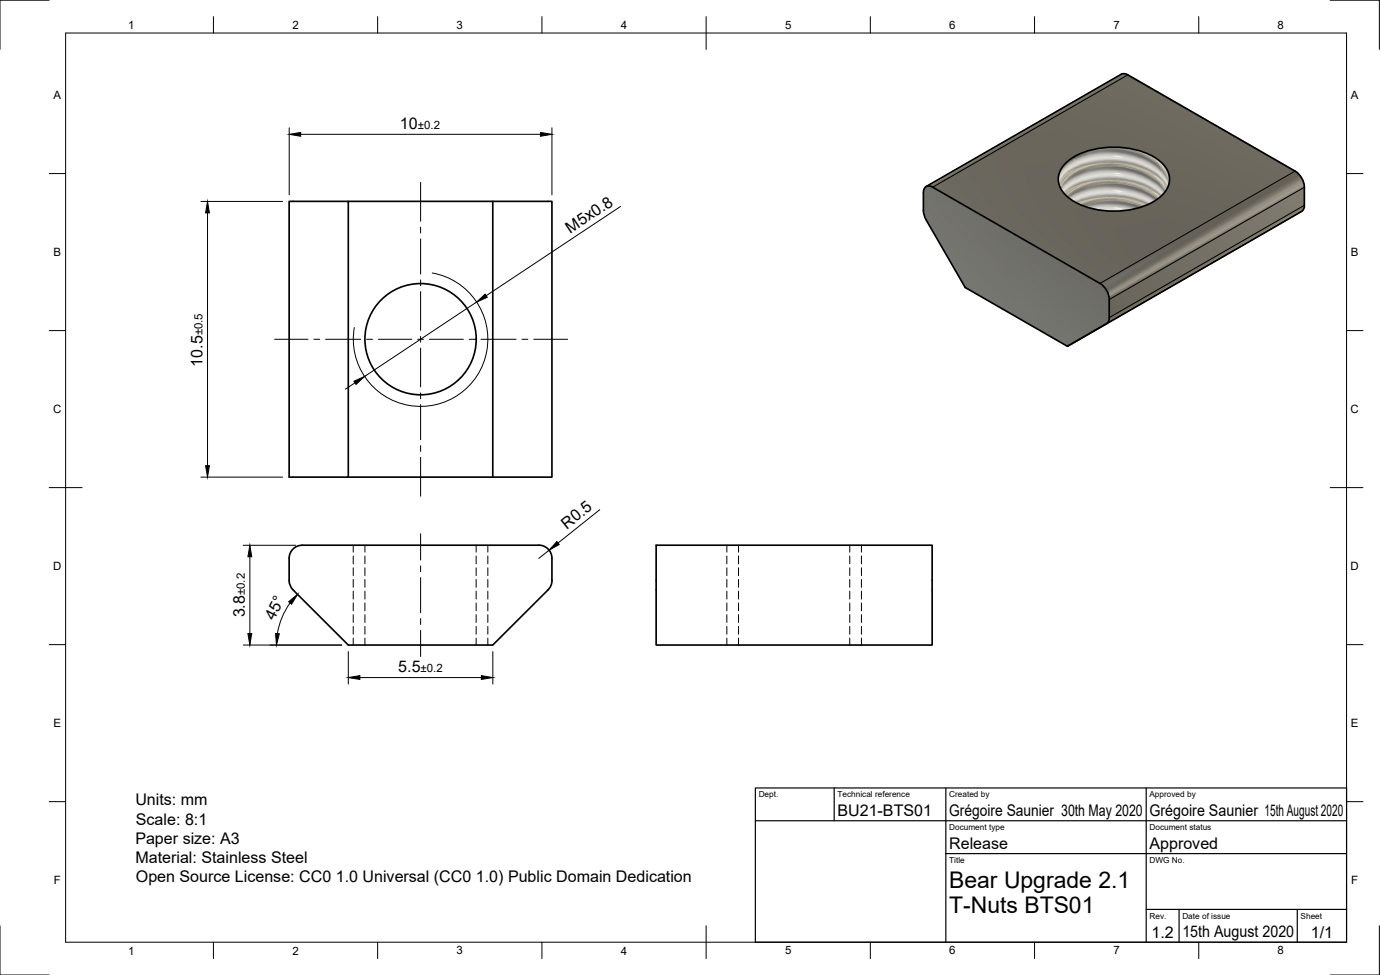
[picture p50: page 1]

Dept. | Technical reference BU21-BTS01 | Created by Grégoire Saunier 30th May 2020 | Approved by Grégoire Saunier 15th August 2020

Units: mm
Scale: 8:1
Paper size: A3
Material: Stainless Steel
Open Source License: CC0 1.0 Universal (CC0 1.0) Public Domain Dedication

Document type Release | Document status Approved

Title Bear Upgrade 2.1 T-Nuts BTS01 | DWG No.

Rev. 1.2 | Date of issue 15th August 2020 | Sheet 1/1

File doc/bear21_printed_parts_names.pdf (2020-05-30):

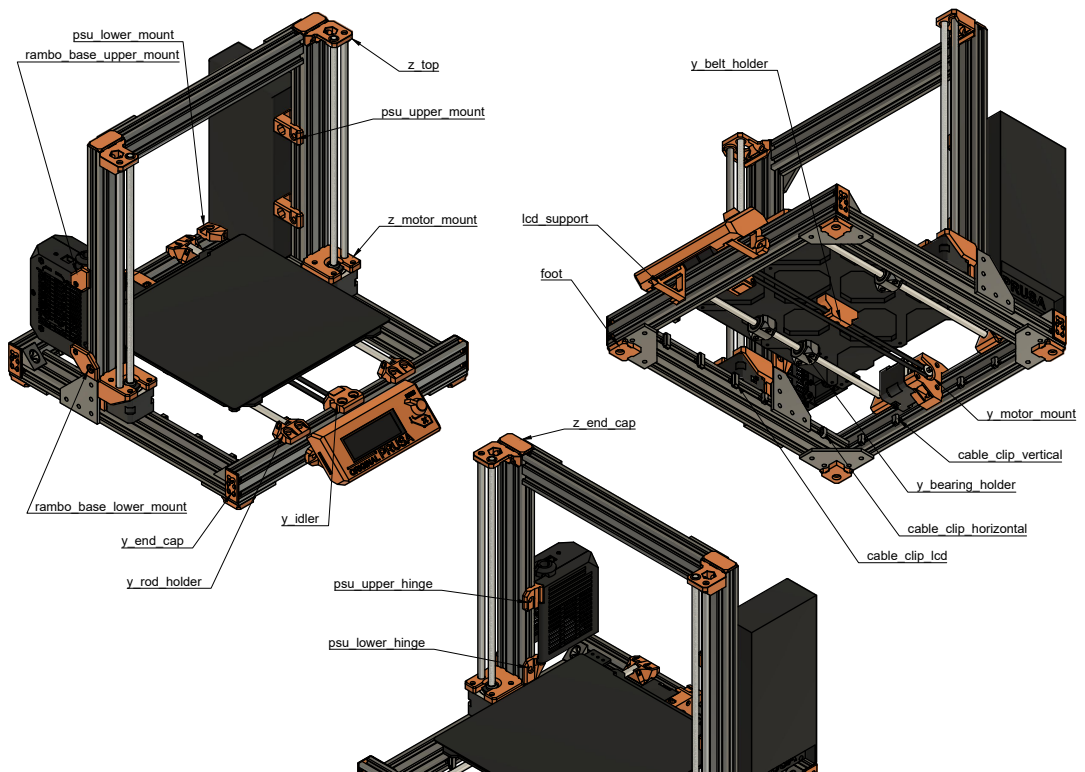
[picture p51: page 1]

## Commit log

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2017-10-01 switch to i3 bear upgrade, reuse original frame to lower the price
    [drilling_helper.step, drilling_helper.stl, end_cap.step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]
2017-10-01 reduce material and improve shape for better precision
    [drilling_helper.step, drilling_helper.stl]
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2017-10-02 fix link to stl files
2017-10-03 fix wrong v-slot length detail
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2017-10-04 fix screw head issue and make part easier to print
    [prusa_i3_bear_upgrade.f3z, rod_holder_back.step, rod_holder_back.stl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]
2017-10-04 reduce nut pockets and make print a bit easier to print
    [prusa_i3_bear_upgrade.f3z, psu_lower_mount.step, psu_lower_mount.stl]
2017-10-05 fix issue with M4 nut. shape better aligned to psu. reinforce psu_lower_mount
    [psu_lower_mount.step, psu_lower_mount.stl, psu_upper_mount.step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]
2017-10-05 switch to single rod_holder. make part adjustable with rod length
    [rod_holder.step, rod_holder.stl, rod_holder_back.step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]
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2017-10-07 rework psu mounts. This closes #2
    [psu_lower_mount.step, psu_lower_mount.stl, psu_upper_mount.step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]
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2017-10-07 update y_idler : better resist to thight screwing. improve rail profile
    [y_idler.step, y_idler.stl]
2017-10-08 y_motor_mount: fix issue where M5x12mm was too short, now use 15mm. improve rail profile and screws holes/heads. Add selective infill
    [y_motor_mount.step, y_motor_mount.stl]
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2017-10-09 lcd_supports : reinforce frame mounting part. increase size of polygon and remove chamfers to reduce material
    [lcd_support_a.step, lcd_support_a.stl, lcd_support_b.step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]
2017-10-09 fix issue where holes where cracking too easily
    [end_cap.step, end_cap.stl]
2017-10-10 drilling helper : it is now possible to test the fit if the printer is not disassembled. Improve holes size and fitting
    [drilling_helper.step, drilling_helper.stl]
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2017-10-27 improve selective infill. improve top of vertical screw holes to avoid cleaning after printing. rod diameter reduced by 0.05
    [lcd_support_a.step, lcd_support_a.stl, lcd_support_b.step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]
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2017-10-30 add z-top-fix
    [z_top_fix_1.2.f3d, z_top_fix_1.2.step, z_top_fix_1.2.stl]
2017-10-30 add known issue and alu_frame.dxf
    [alu_frame.dxf]
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2017-11-09 remove black angle corner on alum frame
    it is too hard to square and tight the build properly with black angle corner. Removing them makes build easier, cheaper and does not impact rigidity
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2017-11-11 switch from M3 self threading to M3 nuts
    [psu_lower_mount.step, psu_lower_mount.stl]
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2017-11-15 fix psu_upper_mount screws length
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2017-11-20 reduce thickness for m5 screws. improve selective infills. nicer shape
    [rod_holder.step, rod_holder.stl]
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2017-11-29 stronger and better suited for 10mm length screw
    [y_idler.step, y_idler.stl]
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2017-12-14 add selective infill. similar shape between two hinges
    [rambo_lid_lower_hinge.step, rambo_lid_lower_hinge.stl, rambo_lid_upper_hinge.step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]
2017-12-14 use same screw than other rambo mounts. nicer shape
    [rambo_base_upper_mount.step, rambo_base_upper_mount.stl]
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2017-12-14 rambo lid mounts are now on the other side of the vslot
    [rambo_lid_lower_hinge.step, rambo_lid_lower_hinge.stl, rambo_lid_upper_hinge.step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]
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2017-12-15 fix margins/tolerances between printed part and vslot
    [rambo_base_upper_mount.step, rambo_base_upper_mount.stl, rambo_lid_lower_hinge.step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]
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2017-12-16 update tolerances
    [rambo_base_lower_mount.step, rambo_base_lower_mount.stl]
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2017-12-21 now common to all printer versions. stronger and smaller
    [rod_holder.step, rod_holder.stl]
2017-12-27 y motor mount now use M5x12 screws. better rail profile
    [y_motor_mount.step, y_motor_mount.stl]
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2017-12-28 reduce material, closer to MK2s version, improve selective infill
    [lcd_support_a.step, lcd_support_a.stl, lcd_support_b.step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]
2017-12-28 y_motor_mount and y_idler is a different on MK3
    [y_idler.step, y_idler.stl, y_motor_mount.step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]
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2017-12-28 improve rail profile. clean top for M5 hole
    [rambo_lid_lower_hinge.step, rambo_lid_lower_hinge.stl]
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2017-12-29 improve rail profile. improve selective infill. reduce material
    [y_idler.step, y_idler.stl]
2017-12-29 switch to m5x10. add selective infill. improve rail profiles
    [z_motor_mount_front.step, z_motor_mounts.step, z_motor_mounts.stl]
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2017-12-31 improve dimensions according to MK2s. M3 screw head hidden
    [y_idler.step, y_idler.stl]
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2018-01-11 z axis is different for mk3. improve frame holes and back depth
    [z_motor_mount_front.step, z_motor_mount_front.stl, z_motor_mounts.step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]
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2018-01-15 add selective infill on base. frame hole base increased to hide the t-nut. better printed angle
    [rambo_base_upper_mount.step, rambo_base_upper_mount.stl]
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2018-01-16 z axis depth is same as original printer
    [z_motor_mounts.step, z_motor_mounts.stl, z_tops.step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]
2018-01-16 z axis depth is same as original printer. fix mk2 z_motor_mount step export
    [z_motor_mounts.step, z_motor_mounts.stl, z_tops.step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]
2018-01-16 fix uncopied mk2.5 files
    [z_motor_mounts.step, z_motor_mounts.stl, z_tops.step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]
2018-01-16 fix frame hole depth
    [z_motor_mounts.step, z_motor_mounts.stl]
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2018-01-17 avoid nut falling while screwing psu. same shape as mk3 psu lower mount
    [psu_lower_mount.step, psu_lower_mount.stl]
2018-01-17 add chamfer to avoid elephant foot
    [psu_lower_mount.step, psu_lower_mount.stl]
2018-01-17 fix psu hole printed in air
    [psu_lower_mount.step, psu_lower_mount.stl]
2018-01-17 cavity for psu holes nuts. improved rail profile
    [psu_lower_mount.step, psu_lower_mount.stl]
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2018-01-17 fix wrong file
    [psu_lower_mount.step, psu_lower_mount.stl]
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2018-01-17 fix wrong depth
    [psu_lower_mount.step, psu_lower_mount.stl]
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2018-01-18 stronger. improve rod hole. material saving on frame hole
    [z_motor_mount_front.step, z_motor_mount_front.stl, z_motor_mounts.step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]
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2018-01-24 update rod holders to get nicer/round measurements during build phase
    [rod_holder.step, rod_holder.stl]
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2018-01-24 add temporary doc, manual, readme, img and optional parts
    [igus_y_holder_rj4jp-01-08.f3d, igus_y_holder_rj4jp-01-08.step, igus_y_holder_rj4jp-01-08.stl]
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2018-01-26 update z_motor_mount to fix Prusa issue https://github.com/prusa3d/Original-Prusa-i3/issues/49
    [z_motor_mount_front.stl, z_motor_mounts.step, z_motor_mounts.stl]
2018-01-28 improve m3 nut hole for better alignement of the m3 screw. stronger pulley arms
    [y_idler.step, y_idler.stl]
2018-01-28 gives more room to adjust motor against the frame
    [y_motor_mount.step, y_motor_mount.stl]
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2018-01-31 improve print quality inside the smooth rod hole, make Nema 17 a bit more tighten
    [z_motor_mounts.step, z_motor_mounts.stl]
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2018-02-13 fix issue where Z motors where it was not possible to mount them due. Also move them at exact same position as MK2(s)
    [rambo_base_lower_mount.step, rambo_base_lower_mount.stl, rambo_lid_lower_hinge.step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]
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2018-02-13 improve alignement with RAMBo base cover. Add selective infill. Screw a bit higher to ease mounting
    [rambo_base_upper_mount.step, rambo_base_upper_mount.stl]
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2018-02-13 remove tabs. add margin for bed alignment measurement during calibration
    [psu_upper_mount.step, psu_upper_mount.stl]
2018-02-13 add margin with bottom left vslot. M3 hole through all the mount
    [psu_lower_mount.step, psu_lower_mount.stl]
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2018-02-14 reduce/optimize height of Z motor mount and rod holders
    [rod_holder.step, rod_holder.stl, z_motor_mounts.step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]
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2018-02-14 shorter by 0.25mm
    [y_idler.step, y_idler.stl]
2018-02-14 fix constraints
    [y_idler.step, y_idler.stl]
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2018-02-15 adapt height to latest rod holder version and add chamfer on M3 nut
    [rambo_base_upper_mount.step, rambo_base_upper_mount.stl]
2018-02-15 now use 3 fixations instead of 4
    [end_cap.step, end_cap.stl]
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2018-02-15 tighter PCB fixation
    [lcd_support_a.step, lcd_support_a.stl, lcd_support_b.step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]
2018-02-15 fix hinge support
    [rambo_lid_lower_hinge.step, rambo_lid_lower_hinge.stl]
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2018-02-15 improve print settings, fix vslot length and M3x12 screws
2018-02-15 fix num of M5x10/12 screws and link to stl
2018-02-15 fix link to stl
2018-02-15 was too high by 2.6mm
    [y_motor_mount.step, y_motor_mount.stl]
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2018-02-15 easier to bolt against frame and RAMBo cover
    [rambo_base_lower_mount.step, rambo_base_lower_mount.stl, rambo_base_upper_mount.step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]
2018-02-15 fix Z axis distance to copy MK2s
    [z_tops.step, z_tops.stl]
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2018-02-17 raised by 2.6mm according to new Z motor mount
    [rod_holder.step, rod_holder.stl]
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2018-02-21 M3 screw hole uncovered. fix selective infill
    [rambo_base_upper_mount.step, rambo_base_upper_mount.stl]
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2018-02-21 fix screws
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2018-02-23 remove wrong step about motor cables
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2018-02-25 fix wrong v-slot length
2018-02-25 update PSU dimensions according to issue #11
    [psu_lower_mount.step, psu_lower_mount.stl]
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2018-02-26 remove useless pics in mk2.5 and fix wrong v-slot length
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2018-02-26 fix M5 screw length
2018-02-26 y_motor_mount should be fixed before motor
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2018-02-28 fix missing export
    [y_motor_mount.step, y_motor_mount.stl]
2018-02-28 fix export issue. related to issue #16
    [y_idler.step, y_idler.stl]
2018-03-13 add new Y bearing older. Readme now linked to Thingiverse for single update on changes
    [igus_y_holder_rj4jp-01-08.f3d, igus_y_holder_rj4jp-01-08.step, igus_y_holder_rj4jp-01-08.stl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]
2018-03-13 wrong export, was not the latest version
    [y_bearing_holder.f3d, y_bearing_holder.step, y_bearing_holder.stl]
2018-03-25 switch to exact number of pce. add recommended spares. add self tapping screw. this closes issue #21
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2018-03-25 add z axis end caps. this closes issue #17
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2018-04-07 remove z motor mount to avoid confusion
2018-04-07 add end caps z axis for full upgrade. add quantity in print settings for readability. Minor fixes. This closes #25
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2018-04-30 remove wrong current status
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2018-05-08 fix printer vesion
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2018-05-17 add margin with top of vslot in case of too short cut. improve Z rod hole
    [z_tops.step, z_tops.stl]
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2018-05-17 avoid sharp angle inside Z rod holes to get nicer print
    [z_tops.step, z_tops.stl]
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2018-05-23 add memo on angle cut issue
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2018-05-25 add link to v-slot tolerances
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2018-08-09 fix M5 screws number
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2018-10-07 Fix #62: Assembly instructions step 10 erroneously specify to mount an endstop (MK3 Full)
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2018-11-13 add missing diameter for set screw
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2019-01-31 Fix incorrect screw size for mounting of PSU to PSU lower mount (original M3x10 is too short).
2019-02-01 Fix 'tensionerr' to 'tensioner' in optional parts
2019-02-06 MK3 use shorter PSU M4 screws
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2019-04-05 fix filing of 90deg plates and Z axis tapped holes for official kit
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2019-08-18 fix description and guides according to latest version
    [build_helper_106mm.f3d, build_helper_106mm.stl, build_helper_96mm.f3d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]
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2019-08-19 fix vertical hole orientation
    [y_idler_mount.stl, y_idler_tensioner.stl, y_motor_mount.stl]
2019-08-19 fix print orientation
    [y_motor_mount.stl]
2019-08-19 fix vertical hole
    [y_idler_tensioner.stl]
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2019-08-22 fix orientation
    [y_belt_holder.stl]
2019-08-23 apply rework from MK3 bearing holder
    [y_bearing_holder.stl]
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2019-09-03 stiffer rambo cover mounts
    [rambo_base_lower_mount.stl, rambo_base_upper_mount.stl]
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2019-09-03 thicker shim for bearing and tighter dowel pin hole
    [y_idler_mount.stl, y_idler_tensioner.stl, y_idler_tensioner_e3d.f3z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]
2019-09-05 increase zip tie strength. better bridging for smooth rod hole. rework selective infill
    [y_rod_holder.stl]
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2019-09-11 rework from scratch due to F360 update issue
    [y_idler_tensioner_e3d.f3z, y_idler_tensioner_e3d.stl]
2019-09-11 reduce delta tension to 2.5mm. narrower opening. stiffer top part of tensioner. screw heads adjustment
    [y_idler_mount.stl, y_idler_tensioner.stl]
2019-09-11 add motor space when pulley is flipped
    [y_belt_holder_bear2.0_mk2s-2.5-2.5s.f3d, y_belt_holder_bear2.0_mk2s-2.5-2.5s.step, y_belt_holder_bear2.0_mk2s-2.5-2.5s.stl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]
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2019-09-12 fix wrong screw length for B01 and B02
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2019-09-14 fix wrong printed parts name
    [y_belt_holder_9mm_belt_bear2.0_mk2s-2.5-2.5s.f3z, y_belt_holder_9mm_belt_bear2.0_mk2s-2.5-2.5s.step, y_belt_holder_9mm_belt_bear2.0_mk2s-2.5-2.5s.stl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]
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2019-09-20 rework hinges to new design style
    [rambo_hinge_lower.stl, rambo_hinge_lower_mk2-2s.stl, rambo_hinge_lower_mk2.5-2.5s.stl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]
2019-09-24 fix wrong orientation of belt holder for MK2S
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2019-10-31 shorter LCD mount
    [lcd_support_a.stl, lcd_support_b.stl]
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2019-11-01 fix issues with derive feature of F360 on Y axis
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2019-11-02 stronger z tops to ensure tightening is square
    [z_tops.stl]
2019-11-02 reduce selective infill to reduce warping
    [z_tops.stl]
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2019-11-04 reduce warping of Z tops
    [z_tops.stl]
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2019-12-10 revert work ongoing on Y belt holder
    [y_belt_holder_9mm_belt_bear2.0_mk2s-2.5-2.5s.stl, y_belt_holder_9mm_belt_bear2.1_mk2s-2.5-2.5s.stl, y_belt_holder_9mm_belt_bear2.1_mk3-3s.stl]
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2019-12-29 reduce thickness for mk3(s). fix bear 2.0 mk2 belt height. stiffer clampig screw mount
    [y_belt_holder.stl, y_belt_holder_9mm_belt_bear2.0_mk2s-2.5-2.5s.f3z, y_belt_holder_9mm_belt_bear2.0_mk2s-2.5-2.5s.stl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]
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2020-01-04 y_bearing_holder: increase nut hole size to be sure nut is going fully down
    [y_bearing_holder.stl]
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2020-01-09 fix stock prusa frame link and add bulb
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2020-02-02 fix hole position on heated bed
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2020-04-24 fix wrong y_rod_holders
    [bear_2.0_mk2_upgrade_to_2.1.step, y_rod_holder.stl]
2020-05-05 add missing step files and rename source folder
    [bear_2.0_mk2_upgrade_to_2.1.step, lcd_cover.step, lcd_cover_assembly.f3z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]
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2020-07-03 wrong screw length for MK2(S)-2.5(S) motor mount
2020-07-04 fix incompatible PSU mounts for MK2_2.0-to-2.1 upgrade
    [psu_lower_mount.stl, psu_upper_mount.stl]
2020-07-04 fix length of build helper for Z axis
    [build_helper_z.stl, build_helper_z_96mm.stl]
2020-07-04 fix sync of build helper Z axis
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2020-07-21 improve cable management for too short cables
    [cable_clip_horizontal.stl, cable_clip_lcd.stl, cable_clip_vertical.stl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]
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2020-08-03 increase tolerances to avoid binding with badly tuned printers
    [z_leadscrew_cap.stl]
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2020-09-21 Add missing washer to Y idler
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
